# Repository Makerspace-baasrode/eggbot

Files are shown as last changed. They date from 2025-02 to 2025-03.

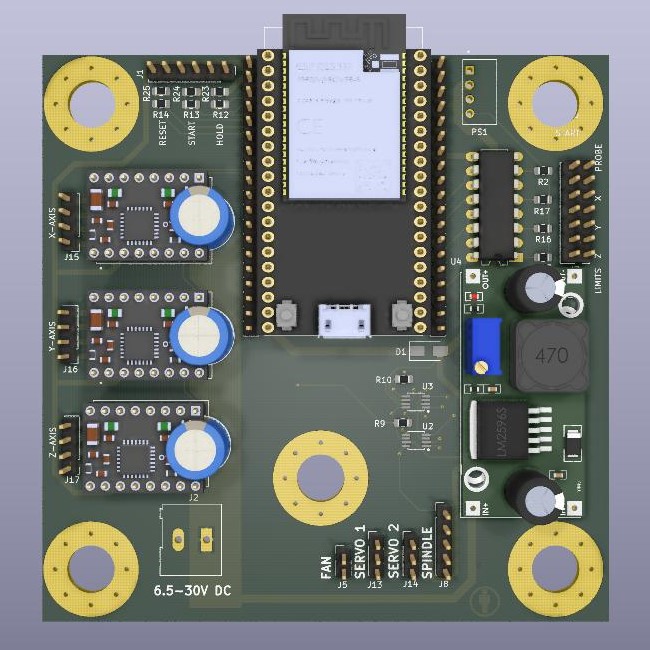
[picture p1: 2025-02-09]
PCB/render/ESP32-cnc.jpg

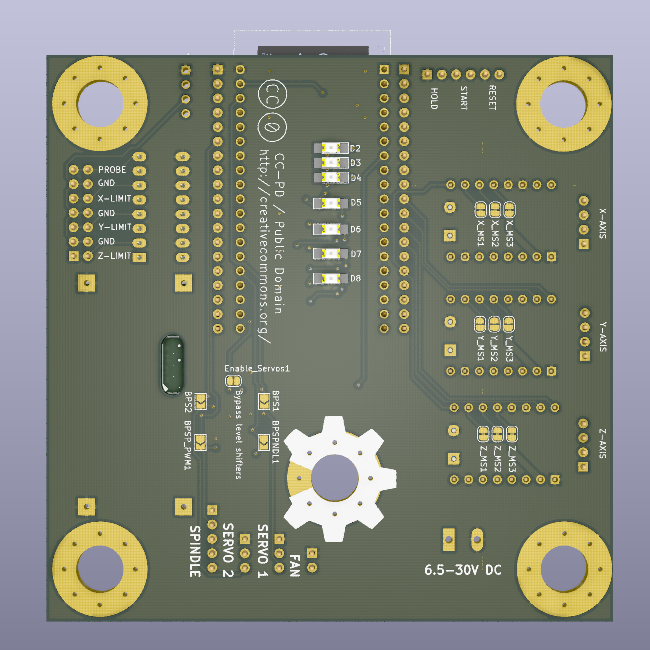
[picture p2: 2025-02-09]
PCB/render/ESP32-cnc_back.png

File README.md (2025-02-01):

# eggbot
a drawing machine using eggs as a canvas

This is a project that started in with a build about 10 years ago.
So in this repository you will find a section of old reference files, of which I can not guarantee that they are still functional. But I rather include them to let you wander around to discover what is our there.
I know that a lot of the software will no longere be functional and needs an update, but I'd liked to keep them here as a reference to what was used 10+ years ago

The new build we are attempting in 2025 will be in the top level. 
It will be structured in the several technices we are going to use, CAD-model, 3D-print, laser cutting, PCB design, PCB assembling, ...

If there is any suggestion to organize it differently please let me know

## original project

this project is a make over of the [Eval Mad Scientists](https://shop.evilmadscientist.com/productsmenu/766) eggbot project. All credits go to them as the originators of the ideas. (https://hackaday.com/2019/04/17/what-can-you-learn-from-an-eggbot/)

## refenced links
### The original
- [The Original Egg-Bot Kit](https://wiki.evilmadscientist.com/The_Original_Egg-Bot_Kit)

### 3D prints
- [Enhanced penholder for SphereBot](https://www.thingiverse.com/thing:13407)
- [Laser Cut Sphere-o-bot](https://www.thingiverse.com/thing:368403#files)
- [Laser Cut Sphere-o-bot Instructables](https://www.instructables.com/Laser-Cut-Sphere-O-Bot/)
- [Fischer Technik Eggbot](https://www.thingiverse.com/thing:8109)
- [Eggcup holders for SphereBot / Completely Printable Eggbot](https://www.thingiverse.com/thing:13960)
- [Completely printable Egg-drawer](https://www.thingiverse.com/thing:7988)
- [Finucane Derivative Eggbot](https://www.thingiverse.com/thing:65753)

### Drawing
- [StippleGen](https://wiki.evilmadscientist.com/StippleGen)
- [StippleGen: Weighted Voronoi](https://www.evilmadscientist.com/2012/stipplegen-weighted-voronoi-stippling-and-tsp-paths-in-processing/)
- [code and designs](https://github.com/davidbliss/eggbot)

### Software
- [SphereBotSenderProcessing](https://github.com/zaggo/SphereBotSenderProcessing)
- [Eggduino](https://github.com/cocktailyogi/EggDuino/)
- [Eggbotsimulator](https://github.com/gabber1/EggbotSimulator)
- [EBB Commands](https://www.schmalzhaus.com/EBB/EBBCommands.html)

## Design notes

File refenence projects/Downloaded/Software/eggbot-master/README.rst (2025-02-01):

Arduino Eggbot
==============

Reference
---------

- Motor Shield v2:
  http://learn.adafruit.com/adafruit-motor-shield-v2-for-arduino/overview
- Stepper motors: http://www.solarbotics.net/library/pdflib/pdf/motorbas.pdf

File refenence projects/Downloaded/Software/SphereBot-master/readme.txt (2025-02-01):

v0.1

This is the firmware for an EggBot-style SphereBot.
The firmware directly interprets GCode send over the serial port.

There will be more information on the SphereBot at http://pleasantsoftware.com/developer/3d (in the near future...)

!!!!!!!!
This sketch needs the following non-standard libraries (install them in the Arduino library directory):
SoftwareServo: http://www.arduino.cc/playground/ComponentLib/Servo
TimerOne: http://www.arduino.cc/playground/Code/Timer1
!!!!!!!!

Copyright 2011 by Eberhard Rensch <http://pleasantsoftware.com/developer/3d>

This program is free software: you can redistribute it and/or modify
it under the terms of the GNU General Public License as published by
the Free Software Foundation, either version 3 of the License, or
(at your option) any later version.

This program is distributed in the hope that it will be useful,
but WITHOUT ANY WARRANTY; without even the implied warranty of
MERCHANTABILITY or FITNESS FOR A PARTICULAR PURPOSE.  See the
GNU General Public License for more details.

You should have received a copy of the GNU General Public License
along with this program.  If not, see <http://www.gnu.org/licenses/>

Part of this code is based on/inspired by the Helium Frog Delta Robot Firmware
by Martin Price <http://www.HeliumFrog.com>

To create tags File: ctags --langmap="C++:+.pde" S*

GCode commands:

G90	Absolut modus
G91	Icremental modus:

M300S0	Servo 0 degree
M300S90	Servo 90 degree

M18	Stepper off

G0X0Y40	Rapid movement (pen 0mm, rotation 40mm)
G1X40Y0 Slower movement (pen 40mm, rotation 0mm)
G1Y10F660 Movement with feed 660mm/s (rotation 10mm)

;	Comment
( .. )	Comment

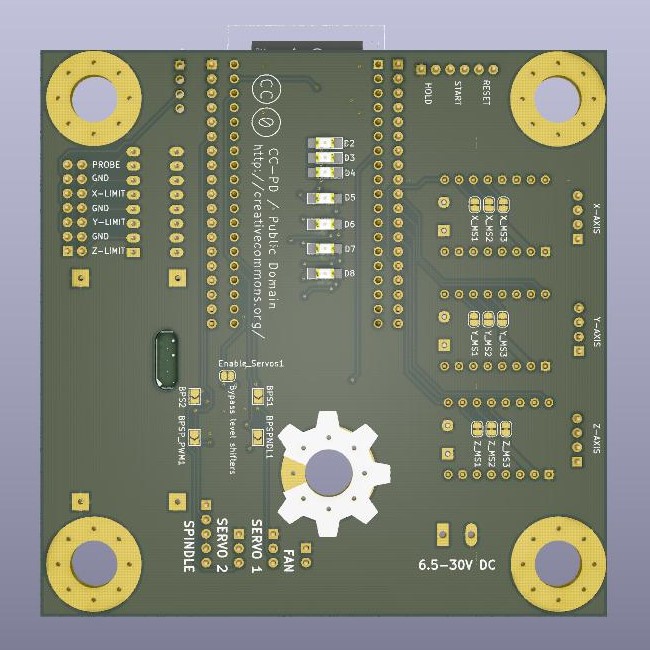
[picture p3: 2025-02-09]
PCB/render/ESP32-cnc_back.jpg

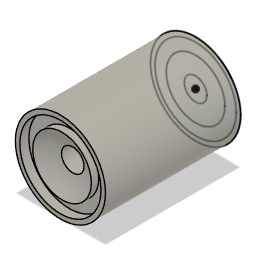
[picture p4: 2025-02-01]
3D CAD model fusion360/_drivecup.a520aff6-5195-480d-919d-d752a0237f96.png

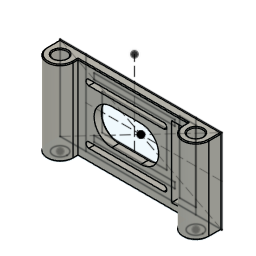
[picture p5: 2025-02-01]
3D CAD model fusion360/_MOTOR BRACKET.0c9dceac-0d53-4d4f-b238-701e19ff46cd.png

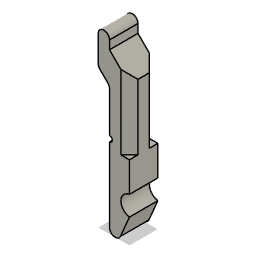
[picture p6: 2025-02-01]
3D CAD model fusion360/_penhouder lever.3cee7135-46d6-436c-b803-6f9b700ddbff.png

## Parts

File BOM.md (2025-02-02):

# BOM

below a bill of materials to build an eggbot.
you still have options to select some of the items. eg. the stepper driver can be any stepper driver with the same footprint as the A4988. 2 types are listed below. You only need 1 type
Cap nuts are included since I like the look of them, but they can be replaced by just normal nuts if you want
O-ring is just and example, if you have 3mm thick o-ring cord you can make them yourself.
The sidepanel can be 3D printed or can be lasercut in acrilyc. That is up to you. The PCB has the same form factor as the sidepanel and can replace 1 of the side panels. If you choose to do so you only need 2 side panels. If you don't like the idea you have to have 3 side panels and an additional 3x M8-nuts
The bearinghouses can be equiped with M4 inserts instead of using standard M4 nuts. This is not in the 3D STL file yet, but if you opt to do so then 8 M4 inserts are needed.
Also the pendrive could be equiped with M4 inserts. Again not in the STL files yet.

The links in the table are just examples no endorsment from my part. They can help you start looking for things. (I have no affiliation with Amazon at all, but it comes handy to show what is needed)

|group|item|quantity|link|
| --- | ---- | --- | --- |
|motor hardware||||
||micro sized servo|1|[AZDelivery 5 x Micro Servo Motor 9G](https://www.amazon.nl/AZDelivery-compatibel-Helikopter-Vliegtuigen-Inclusief/dp/B07CZ42862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)
||nema17 stepper motor|2|[5 stuks, Nema 17, bipolair, 42 Ncm, 1,5 A, 42 x 42 x 39 mm](https://www.amazon.nl/STEPPERONLINE-Stappenmotor-connectoren-3D-printer-CNC-freesmachine/dp/B0B38H2ZMR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)
|electronics||||
||ESP32 dev kit|1|[ESP32 DevKit V4 Ontwikkelingskaart](https://www.amazon.nl/Diymore-Ontwikkelingskaart-ESP32-WROOM-Bluetooth-module-microcontroller/dp/B0C2CRRQCL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)
|stepper driver||||
||TMC2208|2|[BIGTREETECH TMC2209 V1.3 Step-motordriver (6 stuks) 2,8 A](https://www.amazon.com.be/-/nl/Youmile-stappenmotordrivers-koellichaam-schroevendraaier-3D-printermoederborden/dp/B0CD75C83P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)
||TMC2209|2|[Set van 6 TMC2209 V1.3 2,8A](https://www.amazon.com.be/-/nl/Youmile-stappenmotordrivers-koellichaam-schroevendraaier-3D-printermoederborden/dp/B0CD76T6LF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)
||A4988|2|[AZDelivery 5 x A4988 Stappenmotor Driver Module met koellichaam](https://www.amazon.nl/AZDelivery-Stappenmotor-koellichaam-compatibel-Inclusief/dp/B083V59HTB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)
||PCB|1||
|nuts and bolts||||
||threaded rods M8x250mm|3||
||threaded rods M6x250mm|1||
||nuts M8|16 or 19||
||Cap nuts M8|6||
||M4 washer|20||
||M4 bolt x 15|10||
||M4 nut|12||
||M4 inserts|10|[Threaded Insert, M4 x 4 x 6 3D Printing Brass Nuts](https://www.amazon.com/Threaded-Printing-Internal-Embedment-Injection/dp/B0D44KYF8G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)
||M4 bolt x 40|1||
||M4 set bolt|1||
||O-ring 15x3|2|[Othmro Nitril Rubber O-ringen 18mm OD 12mm ID 3.1mm Pack van 50](https://www.amazon.nl/Othmro-ringen-Breedte-Metrische-Afdichtende/dp/B08K7BV6FQ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)
||spring 0.8mm ID 7.2mm L=30mm |1|[Qrity 10 stuks compressieveren, drukveer van roestvrij staal, 1,2 x 10 x 40 mm](https://www.amazon.nl/Qrity-compressieveren-roestvrij-ambachtelijke-reparatie/dp/B0D3TT7JVD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)
||bearing 606zz|2|[10 Stuks 606ZZ Afgedicht Kogellager](https://www.amazon.nl/XiKe-606ZZ-Voorgesmeerd-afdichtingen-Diepgroefkogellager/dp/B07JJC9SFK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)
|3D prints||||
||drive cup|1||
||idler cup|1||
||Bearing house M6|2||
||backpanel|1||
||pen drive|1||
||penarm|1||
||penholder|1||
||penholder lever|1||
||penveer|1||
|lasercuts|||
||sidepanels|2 or 3||

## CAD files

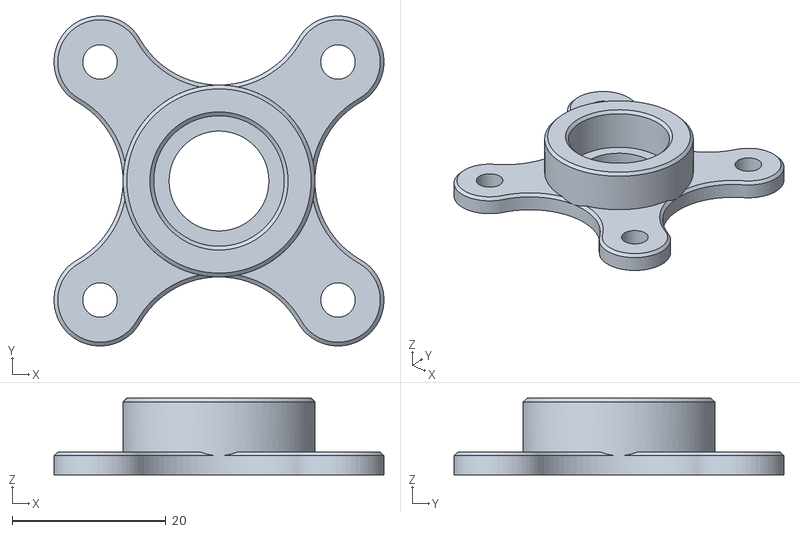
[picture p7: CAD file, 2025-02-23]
3D print models/Bearinghouse M6 V3.stl
43.0 x 43.0 x 10.0

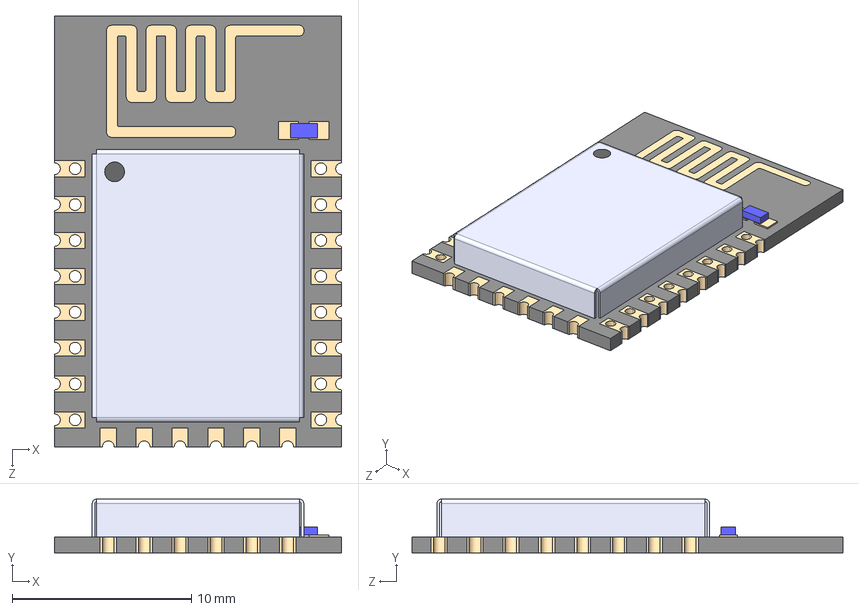
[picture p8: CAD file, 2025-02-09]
PCB/resources/ESP12E/ESP8266-12E_ESP-12E.step
16.0 x 3.00 x 24.0 mm

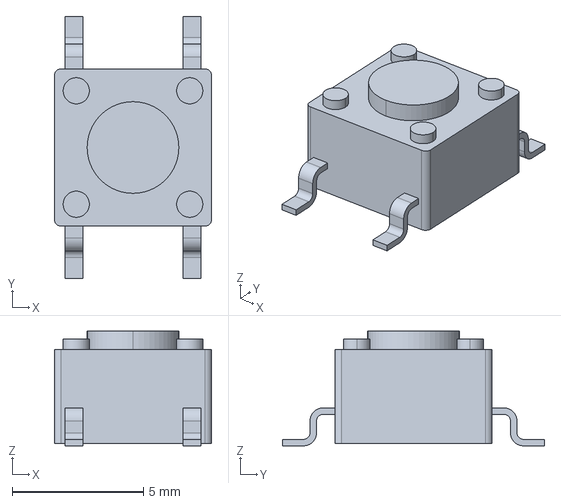
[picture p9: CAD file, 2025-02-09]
PCB/resources/spst-switch/3-1437565-0.step
6.00 x 10.0 x 4.38 mm

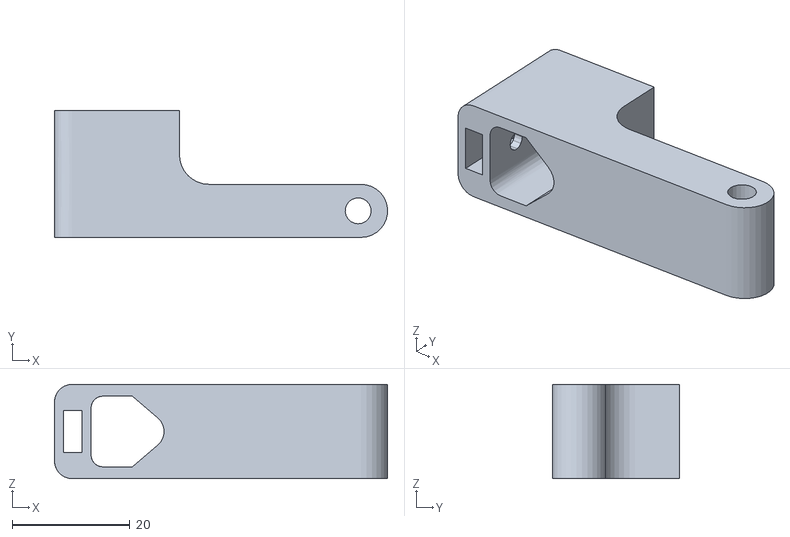
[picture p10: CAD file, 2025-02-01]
refenence projects/Downloaded/Eggbots/Another_spherebot_eggbot_armature/Spherebot_pen.stl
56.5 x 21.5 x 16.0

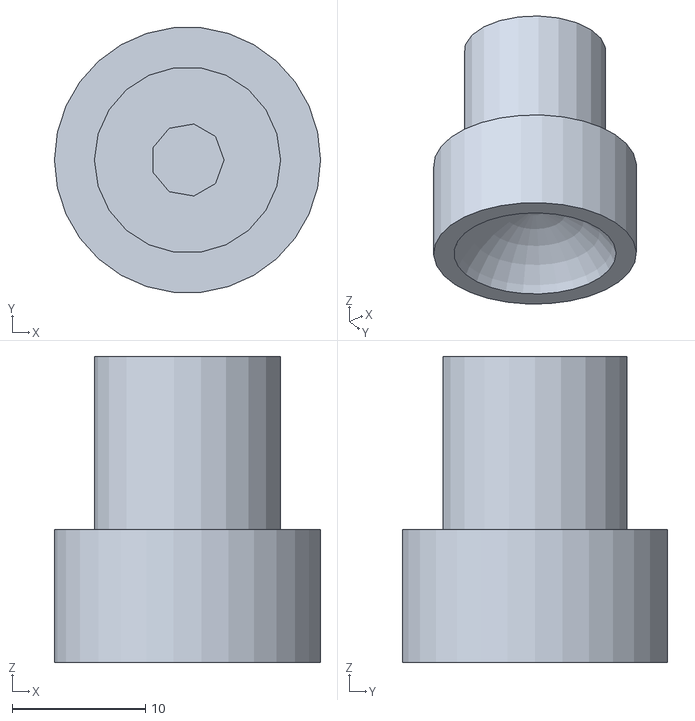
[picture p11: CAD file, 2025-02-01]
refenence projects/Downloaded/Eggbots/Eggcup_holders_for_SphereBot__Completely_Printable_Eggbot/eggcup5mm.stl
20.0 x 19.9 x 23.0

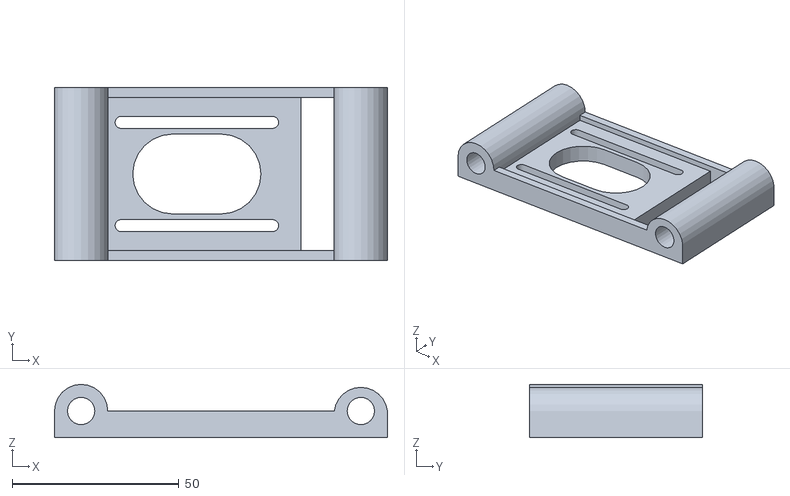
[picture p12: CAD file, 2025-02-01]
refenence projects/Downloaded/Eggbots/Improved_printable_eggbot/back_plate.stl
100.0 x 52.0 x 16.0

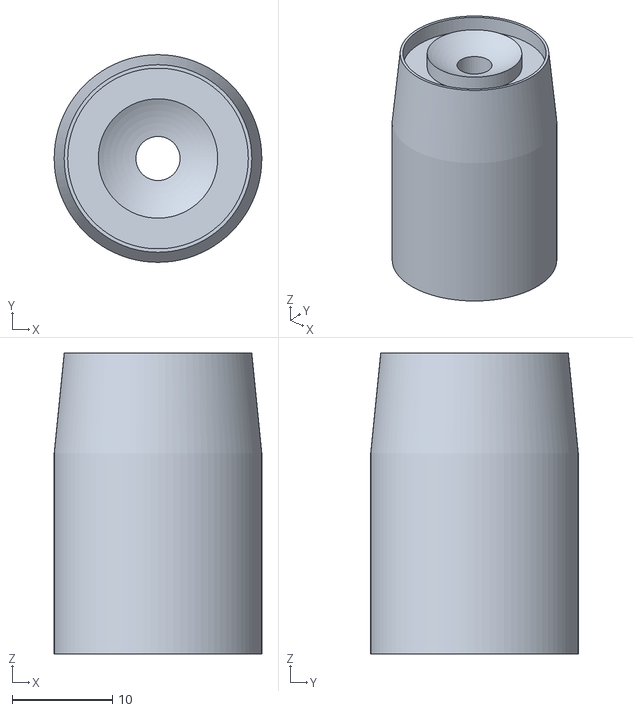
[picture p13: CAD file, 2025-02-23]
3D print models/idler cup V2.stl
20.7 x 20.7 x 30.0

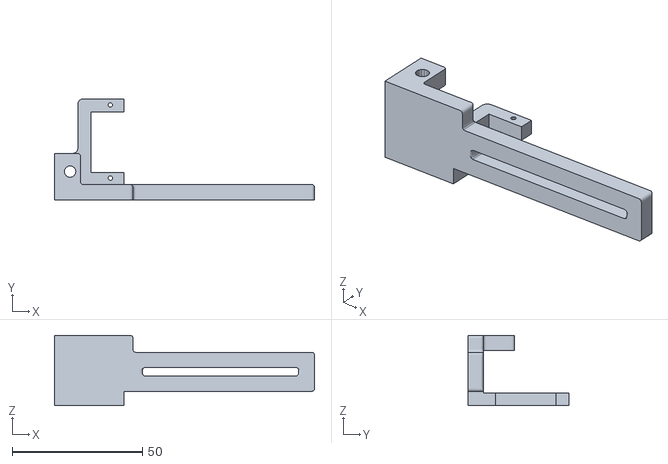
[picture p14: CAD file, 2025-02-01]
refenence projects/Downloaded/Eggbots/Another_spherebot_eggbot_armature/Spherebot_arm.stl
100.0 x 39.0 x 27.0

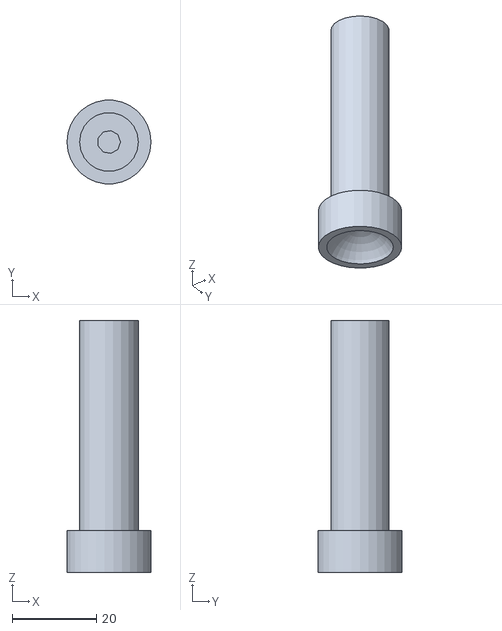
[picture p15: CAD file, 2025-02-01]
refenence projects/Downloaded/Eggbots/Eggcup_holders_for_SphereBot__Completely_Printable_Eggbot/eggcup516.stl
20.0 x 19.9 x 60.0

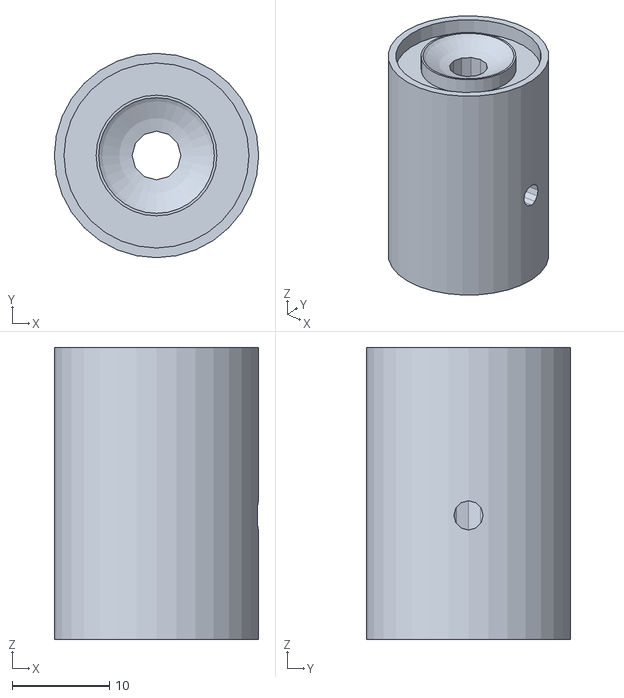
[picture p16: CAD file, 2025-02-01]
refenence projects/Downloaded/Eggbots/Improved_printable_eggbot/drive_cup.stl
21.0 x 21.0 x 30.0

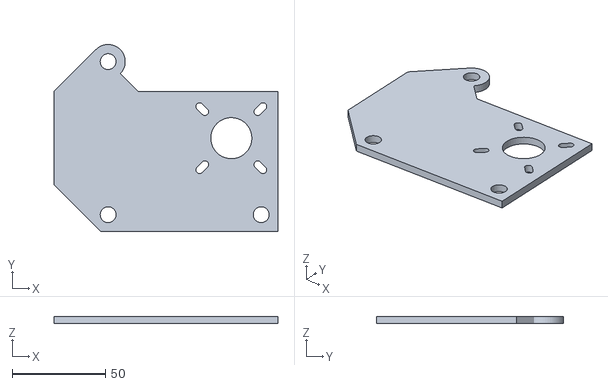
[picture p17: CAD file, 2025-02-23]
3D print models/sidepanel V2.stl
120.0 x 100.2 x 4.00

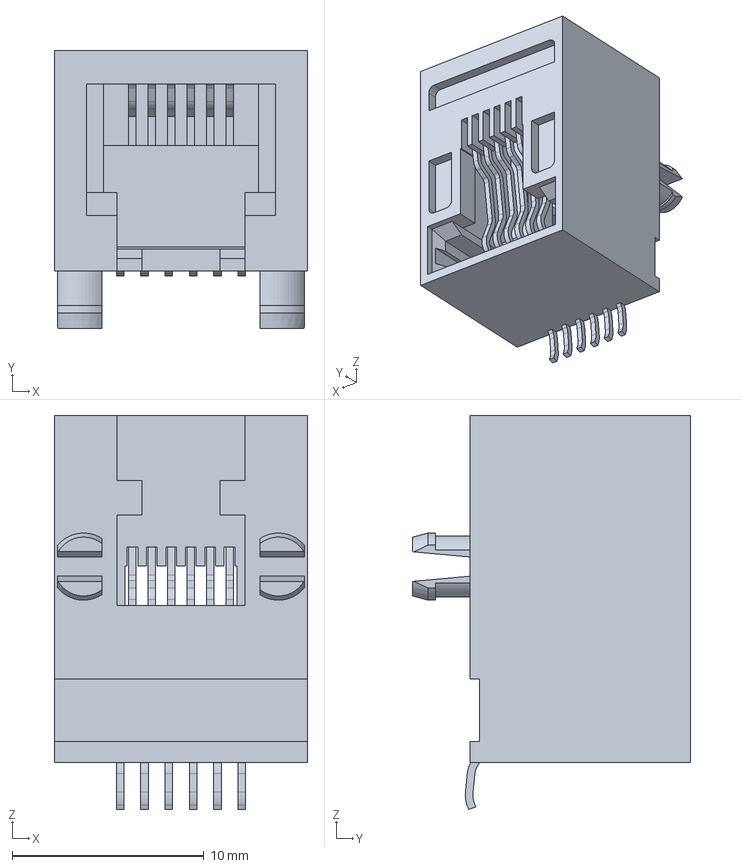
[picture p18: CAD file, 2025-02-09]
PCB/resources/package3d/RJ12.stp
13.2 x 14.5 x 20.6 mm

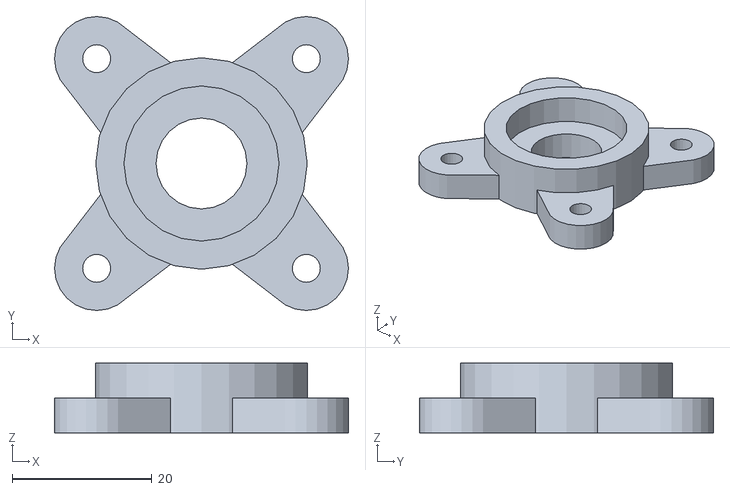
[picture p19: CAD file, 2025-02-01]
refenence projects/Downloaded/Eggbots/Improved_printable_eggbot/idler_bearing_plate.stl
42.1 x 42.1 x 10.0

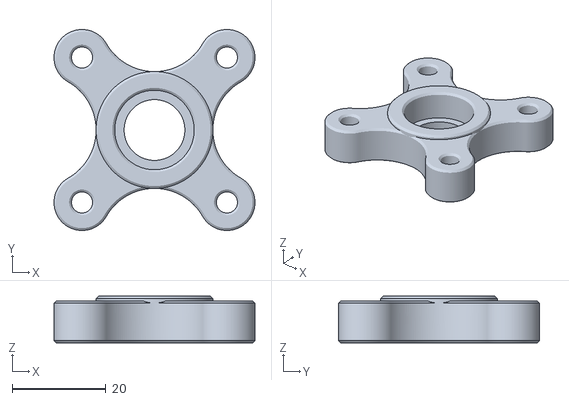
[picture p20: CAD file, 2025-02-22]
3D print models/bearing house M6 inserts V3.stl
43.0 x 43.0 x 10.0

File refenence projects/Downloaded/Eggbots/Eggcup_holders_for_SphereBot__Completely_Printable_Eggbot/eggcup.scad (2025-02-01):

   cupHeight = 10;
   cupDiameter = 20;
   cylDiameter = 14;
   shaftDiameter = 4.9;  // 7.7
   shaftHeight = 50;  // 13
   holeDepth = 10;
   fudge = 0.6;

   difference() {
     cylinder(h = cupHeight, r=cupDiameter/2);
     translate([0,0,-0.4*cupDiameter/2]) { sphere(r=0.9*cupDiameter/2); }
   }
   translate([0,0,cupHeight]) {
   difference() {
       cylinder(h = shaftHeight, r=cylDiameter/2);
       translate([0,0,shaftHeight-holeDepth]) { cylinder(h = shaftHeight+2, r=(shaftDiameter+fudge)/2); }
   }
   }

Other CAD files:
PCB/resources/package3d/8-1437565-0.step
refenence projects/Downloaded/Eggbots/Improved_printable_eggbot/pen_arm_top.stl
3D print models/drivecup_V2.stl
3D CAD model fusion360/BEARINGHOUSE M6 inserts v2.f3d
3D CAD model fusion360/PENDRIVE inserts v1.f3d
3D CAD model fusion360/_BEARINGHOUSE M6.8bb78259-6ec0-4845-8763-fbcfc9640297.f3d
3D CAD model fusion360/_BEARINGHOUSE M8.cff74f27-dfee-4409-ba63-7a86a225738f.f3d
3D CAD model fusion360/_MCMaster.5f8845fe-7c39-4f24-9eef-2dac0d3e2d43.f3d
3D CAD model fusion360/_MOTOR BRACKET.0c9dceac-0d53-4d4f-b238-701e19ff46cd.f3d
3D CAD model fusion360/_PENARM.327dd406-160b-4e44-8dec-6c34584bab60.f3d
3D CAD model fusion360/_PENDRIVE.350a7788-cdd6-4240-858f-49094886f1ab.f3d
3D CAD model fusion360/_SIDEPANEL.0ead6f04-a3f9-46c4-af90-5f052c5ca6cb.f3d
3D CAD model fusion360/_VEER.274ef9a5-93d1-4273-a178-3e04e85e3114.f3d
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

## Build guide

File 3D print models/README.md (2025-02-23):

## What do you need to print :

| Qty | filename |
|-----|---|
| 1x | bearing house M6 inserts V3 |
| 1x | Bearinghouse M6 V3 |
| 1x | drivecup_V2 |
| 1x | idler cup V2 |
| 1x | motor bracket V2 |
| 1x | PENARM |
| 1x | pendrive inserts V2 |
| 1x | penhouder arm |
| 1x | penhouder |
| 1x | penveer |

The side panel can be laser cut or 3D printed. If a laser cutter is available I would go for the acrylic laser cut.

| Qty | filename |
|-----|---|
| 2x | sidepanel V2.dxf laser cut |
| 2x | sidepanel V2.stl 3D print |

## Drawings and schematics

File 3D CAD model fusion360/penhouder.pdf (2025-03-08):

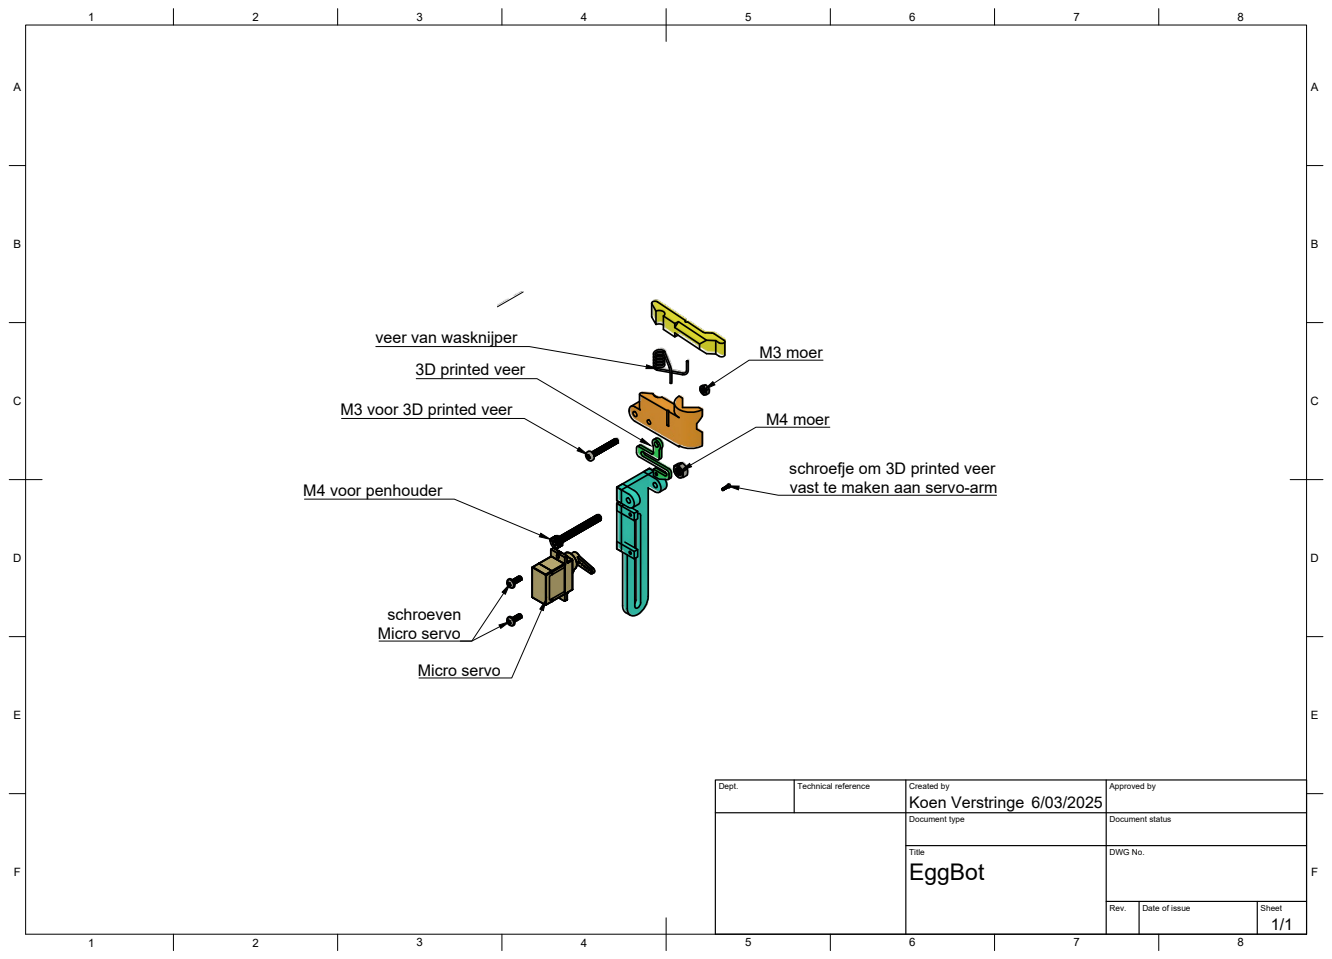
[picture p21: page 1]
Title; DWG No.; Rev.; Date of issue; Sheet; Micro servo; M4 voor penhouder; M3 moer; M4 moer; 3D printed veer

veer van wasknijper

M3 voor 3D printed veer

schroefje om 3D printed veer
vast te maken aan servo-arm

Dept. | Technical reference | Created by Koen Verstringe 6/03/2025 | Approved by

Document type | Document status

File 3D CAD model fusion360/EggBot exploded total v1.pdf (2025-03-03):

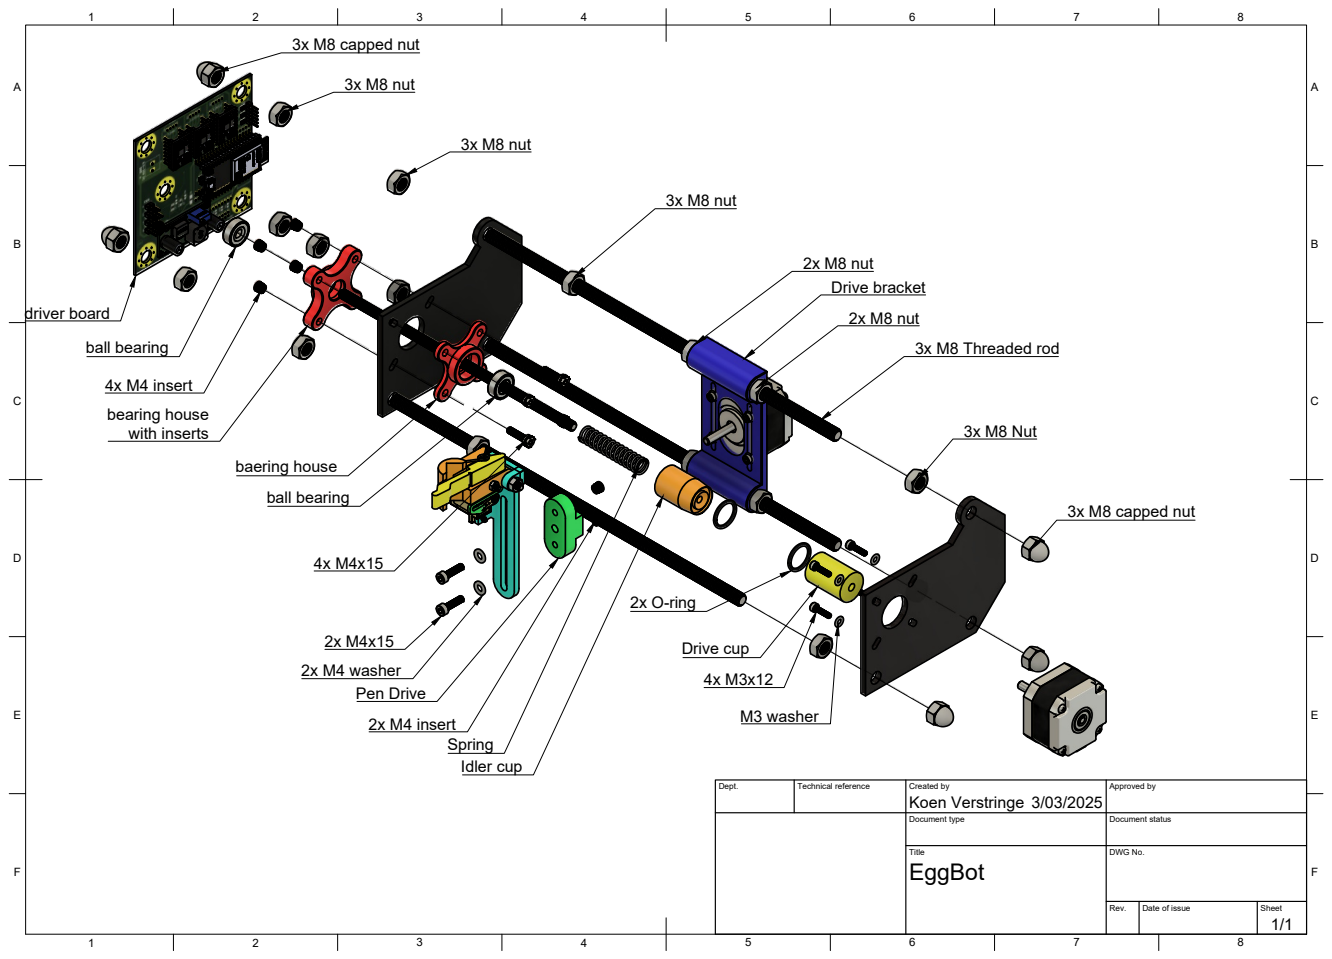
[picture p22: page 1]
Dept.; Technical reference; Created by; Approved by; Document type; Document status; Title; DWG No.; Rev.; Date of issue; Sheet; Koen Verstringe; 3x M8 Nut; 3x M8 capped nut; M3 washer; Drive cup; 2x O-ring; 3x M8 Threaded rod; 2x M4 washer; 2x M4 insert; Pen Drive; 3x M8 nut; 2x M8 nut; Drive bracket; driver board; ball bearing; 4x M4 insert; bearing house with inserts; baering house; Idler cup

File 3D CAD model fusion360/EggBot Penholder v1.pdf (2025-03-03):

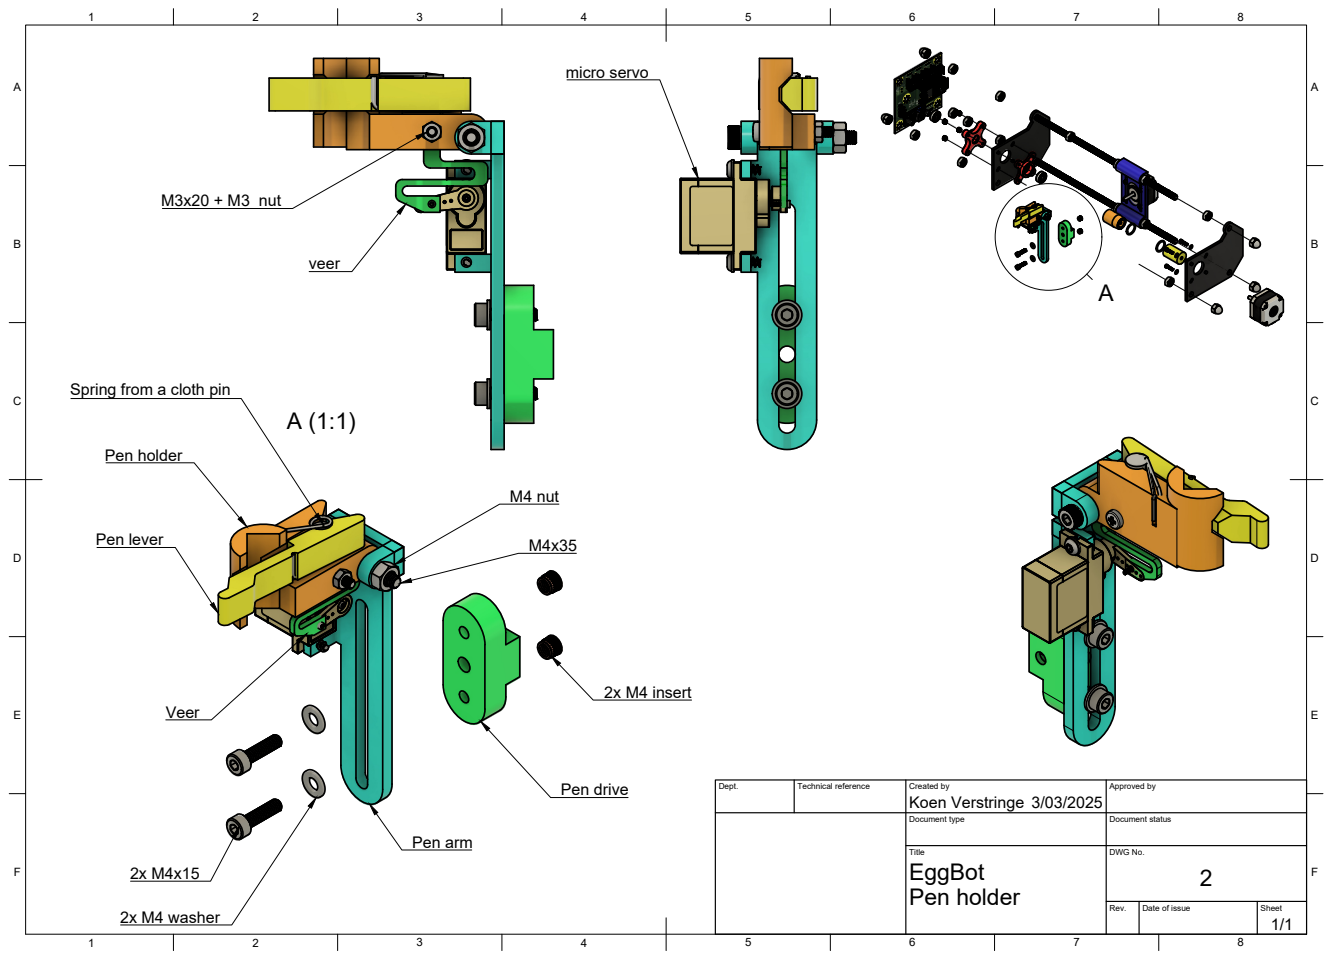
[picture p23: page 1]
Dept.; Technical reference; Created by; Approved by; Document type; Document status; Title; DWG No.; Rev.; Date of issue; Sheet; Pen holder; Koen Verstringe; 2x M4 washer; 2x M4 insert; Pen drive; Pen arm; M4 nut; Pen lever; micro servo; M3x20 + M3 nut

Spring from a cloth pin

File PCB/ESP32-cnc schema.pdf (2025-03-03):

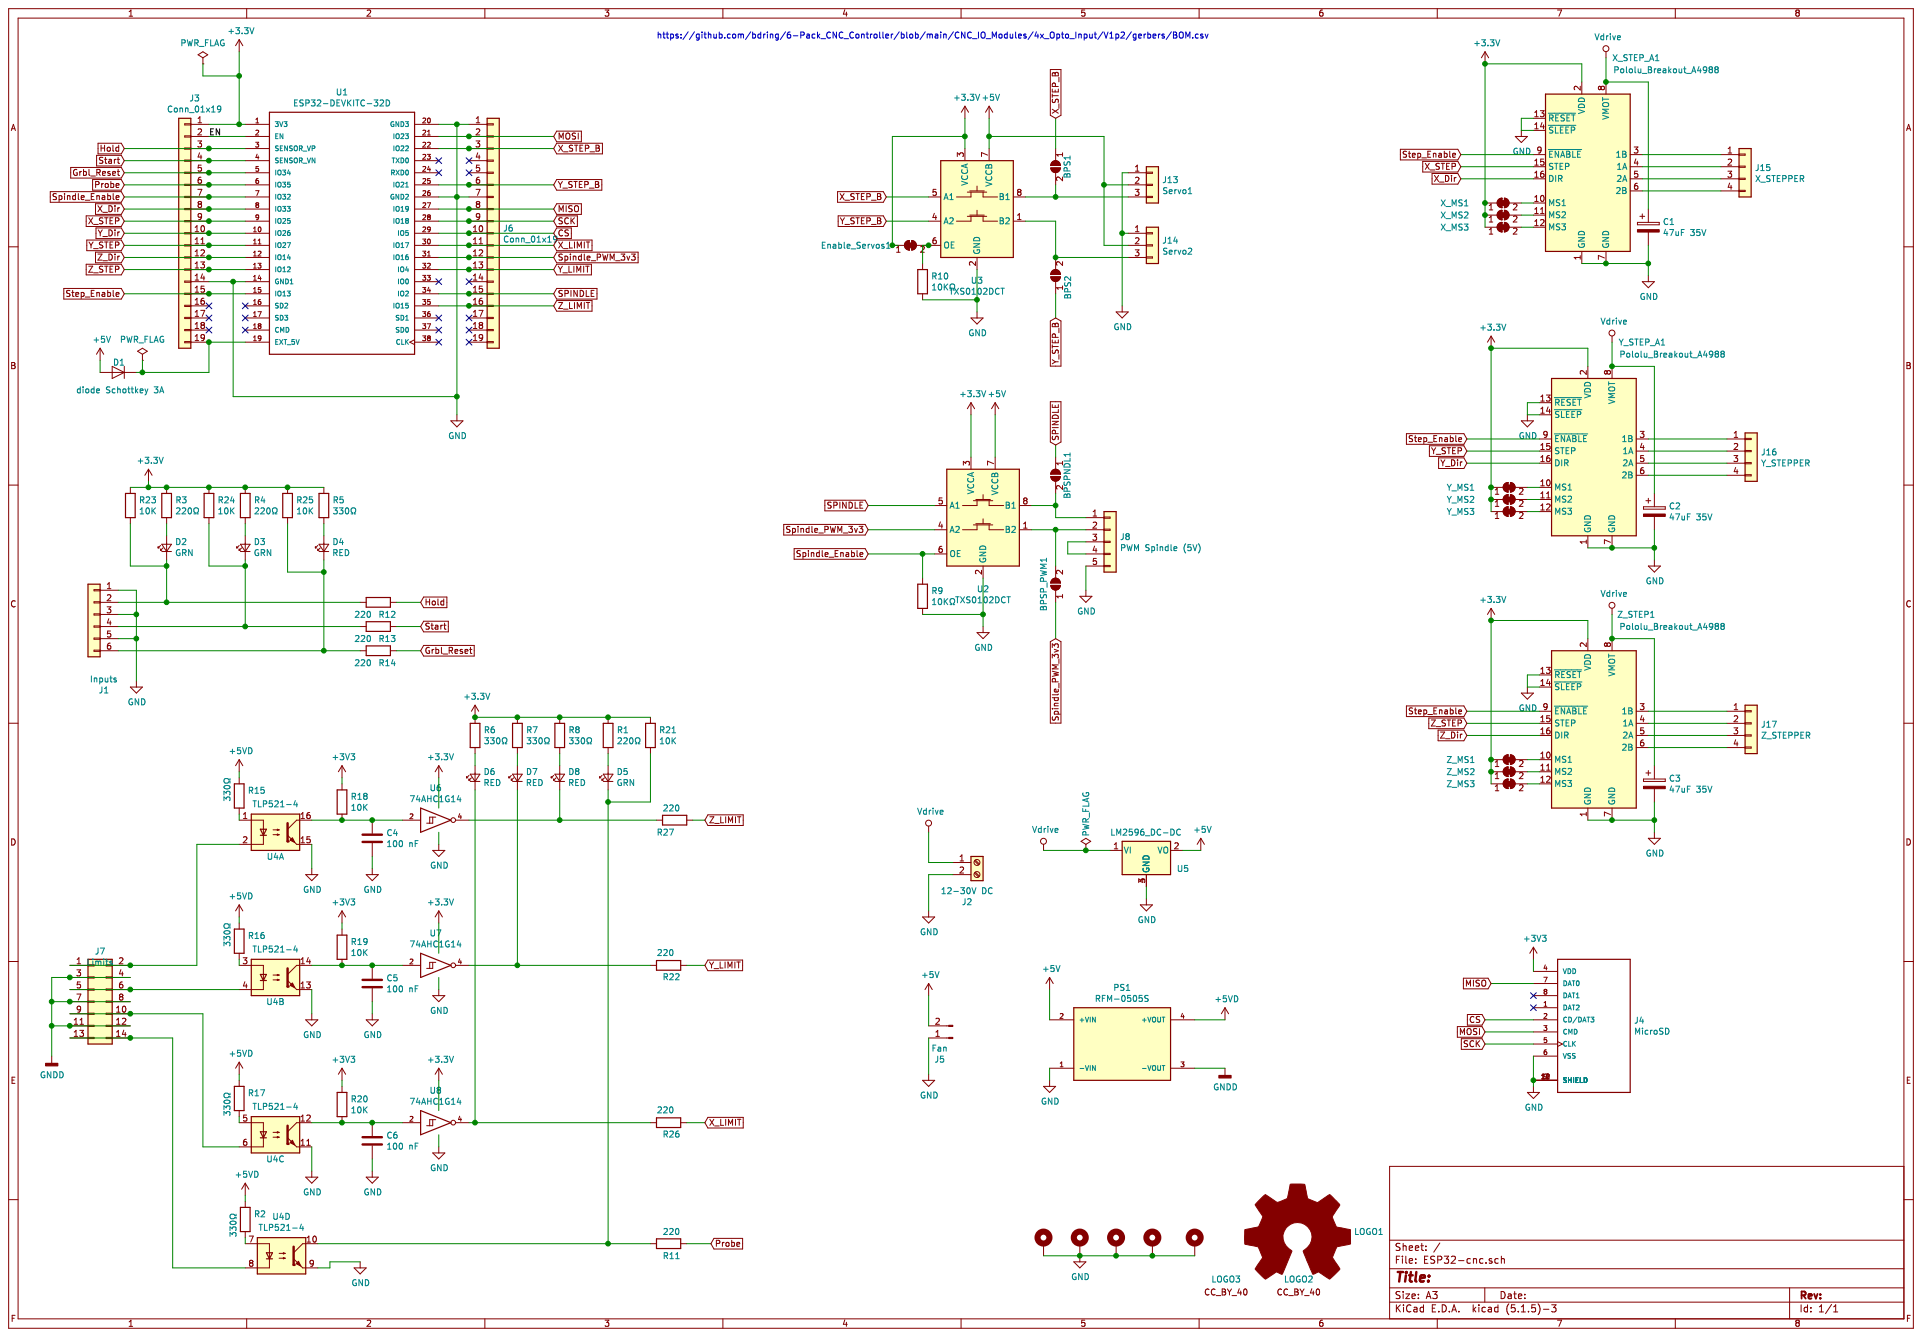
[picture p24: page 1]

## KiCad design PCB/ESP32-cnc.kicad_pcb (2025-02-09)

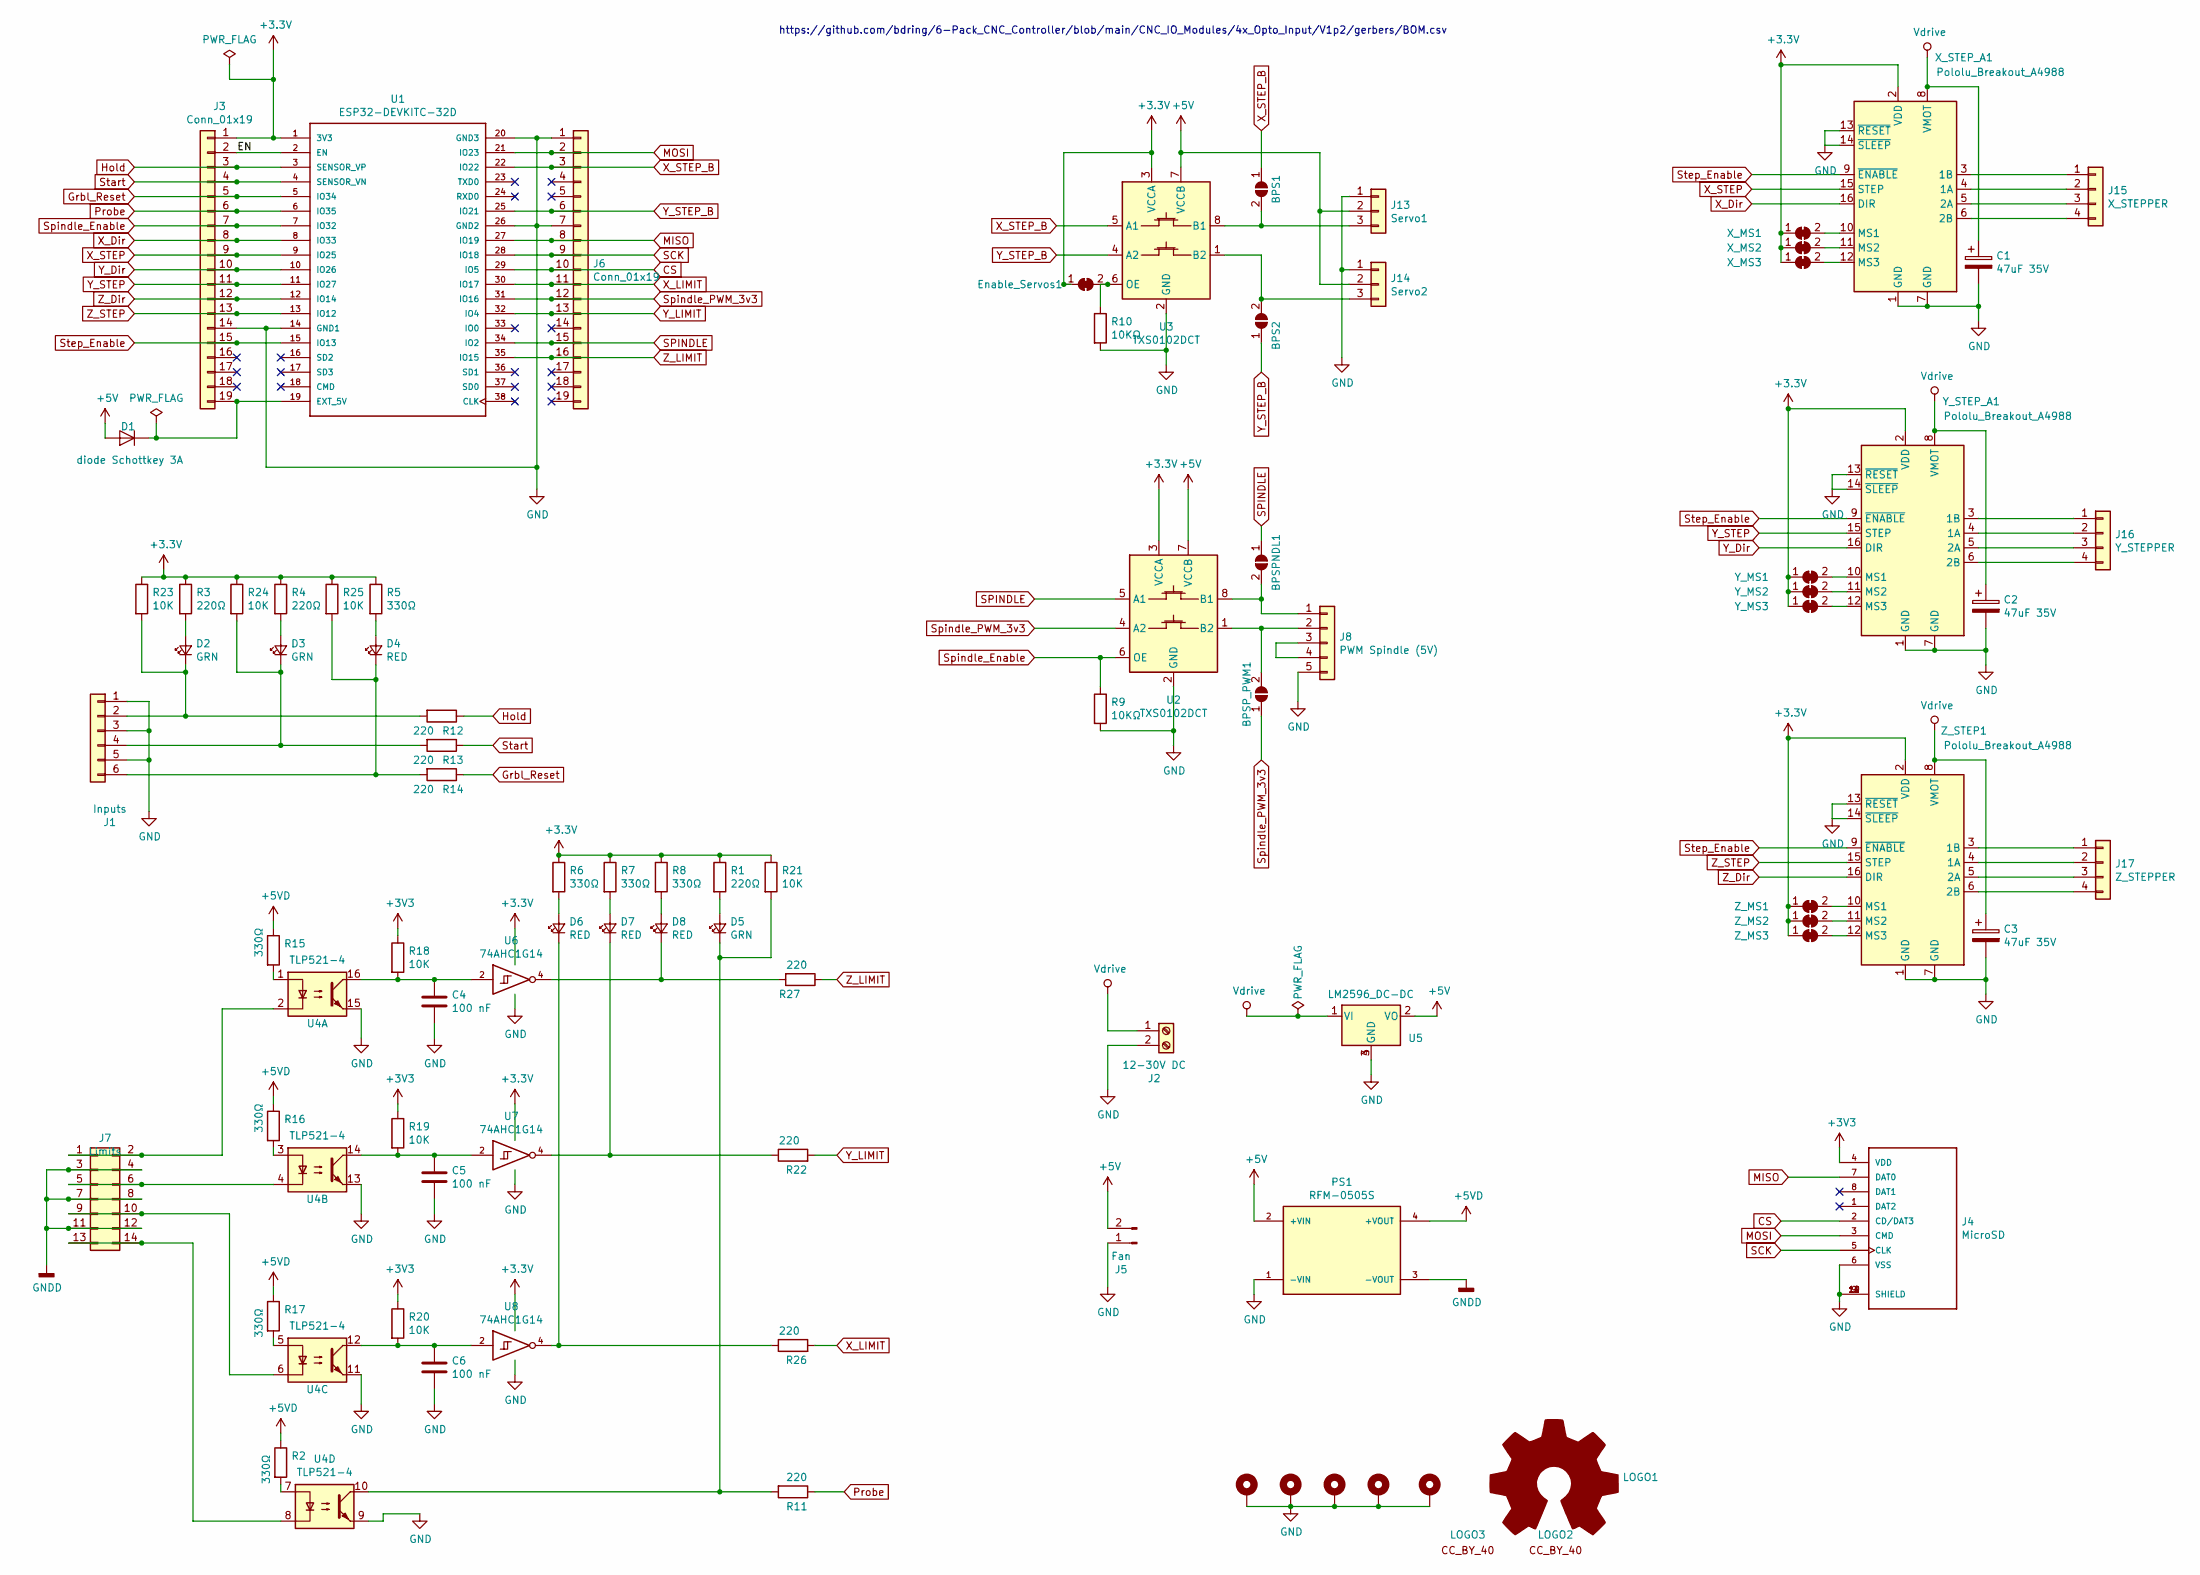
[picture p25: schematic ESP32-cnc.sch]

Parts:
BPS1: SERVO1; SolderJumper-2_P1.3mm_Open_TrianglePad1.0x1.5mm
BPS2: SERVO2; SolderJumper-2_P1.3mm_Open_TrianglePad1.0x1.5mm
BPSPNDL1: SPNDL_ON; SolderJumper-2_P1.3mm_Open_TrianglePad1.0x1.5mm
BPSP_PWM1: SPNDL_PWM; SolderJumper-2_P1.3mm_Open_TrianglePad1.0x1.5mm
C1, C2, C3: 47uF 35V; CP_Radial_D10.0mm_P5.00mm; LCSC C134832
C4, C5, C6: 100 nF; C_0805_2012Metric_Pad1.15x1.40mm_HandSolder
D1: diode Schottkey 3A; D_SMA; LCSC C64982
D2, D3, D5: GRN; LED_1206_HandSoldering
D4, D6, D7, D8: RED; LED_1206_HandSoldering
Enable_Servos1: Enable_Servos; SolderJumper-2_P1.3mm_Bridged_RoundedPad1.0x1.5mm
H1, H2, H3, H4, H5: MountingHole_Pad; MountingHole_8.4mm_M8_Pad_Via
J1: Inputs; PinHeader_1x06_P2.54mm_Vertical
J2: 12-30V DC; TerminalBlock_Altech_AK300-2_P5.00mm
J3, J6: Conn_01x19; PinHeader_1x19_P2.54mm_Vertical
J4: MicroSD; GCT_MEM2067-02-180-00-A_REVB; LCSC C91145
J5: Fan; PinHeader_1x02_P2.54mm_Vertical
J7: Limits; PinHeader_2x07_P2.54mm_Vertical
J8: PWM Spindle (5V); PinHeader_1x05_P2.54mm_Vertical
J13: Servo1; PinHeader_1x03_P2.54mm_Vertical
J14: Servo2; PinHeader_1x03_P2.54mm_Vertical
J15: X_STEPPER; PinHeader_1x04_P2.54mm_Vertical
J16: Y_STEPPER; PinHeader_1x04_P2.54mm_Vertical
J17: Z_STEPPER; PinHeader_1x04_P2.54mm_Vertical
LOGO1: Logo_Open_Hardware_Large; OSHW-Symbol_22.3x20mm_SilkScreen
LOGO2: SYM_CC_BY; Symbol_CreativeCommonsPublicDomain_SilkScreenTop_Small
LOGO3: SYM_CC_BY; Symbol_CC-Attribution_CopperTop_Small
PS1: RFM-0505S; CONV_RFM-0505S; PARTREV 0
R1, R3, R4: 220Ω; R_0805_2012Metric_Pad1.15x1.40mm_HandSolder
R2, R5, R6, R7, R8, R15, R16, R17: 330Ω; R_0805_2012Metric_Pad1.15x1.40mm_HandSolder
R9, R10: 10KΩ; R_0805_2012Metric_Pad1.15x1.40mm_HandSolder; LCSC C140868
R11, R12, R13, R14, R22, R26, R27: 220; R_0805_2012Metric_Pad1.15x1.40mm_HandSolder
R18, R19, R20, R21, R23, R24, R25: 10K; R_0805_2012Metric_Pad1.15x1.40mm_HandSolder
U1: ESP32-DEVKITC-32D; MODULE_ESP32-DEVKITC-32D
U2, U3: TXS0102DCT; SOP65P400X130-8N; LCSC C324082
U4: TLP521-4; DIP-16_W7.62mm_LongPads; lcsc C191333
U5: LM2596_DC-DC; LM2596_DC_DC_Step_Down_Module
U6, U7, U8: 74AHC1G14; SOT-23-5
X_MS1: X_MS1; SolderJumper-2_P1.3mm_Bridged_RoundedPad1.0x1.5mm
X_MS2: X_MS2; SolderJumper-2_P1.3mm_Bridged_RoundedPad1.0x1.5mm
X_MS3: X_MS3; SolderJumper-2_P1.3mm_Bridged_RoundedPad1.0x1.5mm
X_STEP_A1: Pololu_Breakout_A4988; MODULE_A4988_STEPPER_MOTOR_DRIVER_CARRIER
Y_MS1: Y_MS1; SolderJumper-2_P1.3mm_Bridged_RoundedPad1.0x1.5mm
Y_MS2: Y_MS2; SolderJumper-2_P1.3mm_Bridged_RoundedPad1.0x1.5mm
Y_MS3: Y_MS3; SolderJumper-2_P1.3mm_Bridged_RoundedPad1.0x1.5mm
Y_STEP_A1: Pololu_Breakout_A4988; MODULE_A4988_STEPPER_MOTOR_DRIVER_CARRIER
Z_MS1: Z_MS1; SolderJumper-2_P1.3mm_Bridged_RoundedPad1.0x1.5mm
Z_MS2: Z_MS2; SolderJumper-2_P1.3mm_Bridged_RoundedPad1.0x1.5mm
Z_MS3: Z_MS3; SolderJumper-2_P1.3mm_Bridged_RoundedPad1.0x1.5mm
Z_STEP1: Pololu_Breakout_A4988; MODULE_A4988_STEPPER_MOTOR_DRIVER_CARRIER

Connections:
+5V: D1.2 (A), J5.2, J13.2, J14.2, PS1.2 (+VIN), U2.7 (VCCB), U3.7 (VCCB), U5.2 (VO)
+5VD: PS1.4 (+VOUT), R2.1, R15.1, R16.1, R17.1
/EN: J3.2, U1.2 (EN)
CS: J4.2 (CD/DAT3), J6.10, U1.29 (IO5)
GND: C1.2, C2.2, C3.2, C4.2, C5.2, C6.2, H1.1, H2.1, H3.1, H4.1, H5.1, J1.1, J1.3, J1.5, J2.2, J3.14, J4.6 (VSS), J4.9 (SHIELD), J4.10 (SHIELD), J4.11 (SHIELD), J4.12 (SHIELD), J5.1, J6.1, J6.7, J8.5, J13.1, J14.1, PS1.1 (-VIN), R9.2, R10.2, U1.14 (GND1), U1.20 (GND3), U1.26 (GND2), U2.2 (GND), U3.2 (GND), U4.9, U4.11, U4.13, U4.15, U5.3 (GND), U5.4 (GND), U6.3 (GND), U7.3 (GND), U8.3 (GND), X_STEP_A1.1 (GND), X_STEP_A1.7 (GND), X_STEP_A1.13 (~RESET), X_STEP_A1.14 (~SLEEP), Y_STEP_A1.1 (GND), Y_STEP_A1.7 (GND), Y_STEP_A1.13 (~RESET), Y_STEP_A1.14 (~SLEEP), Z_STEP1.1 (GND), Z_STEP1.7 (GND), Z_STEP1.13 (~RESET), Z_STEP1.14 (~SLEEP)
GNDD: J7.3, J7.4, J7.7, J7.8, J7.11, J7.12, PS1.3 (-VOUT)
Grbl_Reset: J3.5, R14.1, U1.5 (IO34)
Hold: J3.3, R12.1, U1.3 (SENSOR_VP)
MISO: J4.7 (DAT0), J6.8, U1.27 (IO19)
MOSI: J4.3 (CMD), J6.2, U1.21 (IO23)
unnamed: BPS1.2 (B), J13.3, U3.8 (B1)
unnamed: BPS2.2 (B), J14.3, U3.1 (B2)
unnamed: BPSPNDL1.2 (B), J8.1, U2.8 (B1)
unnamed: BPSP_PWM1.2 (B), J8.2, U2.1 (B2)
unnamed: C4.1, R18.2, U4.16, U6.2
unnamed: C5.1, R19.2, U4.14, U7.2
unnamed: C6.1, R20.2, U4.12, U8.2
unnamed: D1.1 (K), J3.19, U1.19 (EXT_5V)
unnamed: D2.1 (K), J1.2, R12.2, R23.2
unnamed: D2.2 (A), R3.2
unnamed: D3.1 (K), J1.4, R13.2, R24.2
unnamed: D3.2 (A), R4.2
unnamed: D4.1 (K), J1.6, R14.2, R25.2
unnamed: D4.2 (A), R5.2
unnamed: D5.1 (K), R11.2, R21.2, U4.10
unnamed: D5.2 (A), R1.2
unnamed: D6.1 (K), R26.1, U8.4
unnamed: D6.2 (A), R6.2
unnamed: D7.1 (K), R22.1, U7.4
unnamed: D7.2 (A), R7.2
unnamed: D8.1 (K), R27.2, U6.4
unnamed: D8.2 (A), R8.2
unnamed: Enable_Servos1.2 (B), R10.1, U3.6 (OE)
unnamed: J7.1, J7.2, U4.2
unnamed: J7.5, J7.6, U4.4
unnamed: J7.9, J7.10, U4.6
unnamed: J7.13, J7.14, U4.8
unnamed: J8.3, J8.4
unnamed: J15.1, X_STEP_A1.3 (1B)
unnamed: J15.2, X_STEP_A1.4 (1A)
unnamed: J15.3, X_STEP_A1.5 (2A)
unnamed: J15.4, X_STEP_A1.6 (2B)
unnamed: J16.1, Y_STEP_A1.3 (1B)
unnamed: J16.2, Y_STEP_A1.4 (1A)
unnamed: J16.3, Y_STEP_A1.5 (2A)
unnamed: J16.4, Y_STEP_A1.6 (2B)
unnamed: J17.1, Z_STEP1.3 (1B)
unnamed: J17.2, Z_STEP1.4 (1A)
unnamed: J17.3, Z_STEP1.5 (2A)
unnamed: J17.4, Z_STEP1.6 (2B)
unnamed: R2.2, U4.7
unnamed: R15.2, U4.1
unnamed: R16.2, U4.3
unnamed: R17.2, U4.5
unnamed: X_MS1.2 (B), X_STEP_A1.10 (MS1)
unnamed: X_MS2.2 (B), X_STEP_A1.11 (MS2)
unnamed: X_MS3.2 (B), X_STEP_A1.12 (MS3)
unnamed: Y_MS1.2 (B), Y_STEP_A1.10 (MS1)
unnamed: Y_MS2.2 (B), Y_STEP_A1.11 (MS2)
unnamed: Y_MS3.2 (B), Y_STEP_A1.12 (MS3)
unnamed: Z_MS1.2 (B), Z_STEP1.10 (MS1)
unnamed: Z_MS2.2 (B), Z_STEP1.11 (MS2)
unnamed: Z_MS3.2 (B), Z_STEP1.12 (MS3)
Probe: J3.6, R11.1, U1.6 (IO35)
SCK: J4.5 (CLK), J6.9, U1.28 (IO18)
SPINDLE: BPSPNDL1.1 (A), J6.15, U1.34 (IO2), U2.5 (A1)
Spindle_Enable: J3.7, R9.1, U1.7 (IO32), U2.6 (OE)
Spindle_PWM_3v3: BPSP_PWM1.1 (A), J6.12, U1.31 (IO16), U2.4 (A2)
Start: J3.4, R13.1, U1.4 (SENSOR_VN)
Step_Enable: J3.15, U1.15 (IO13), X_STEP_A1.9 (~ENABLE), Y_STEP_A1.9 (~ENABLE), Z_STEP1.9 (~ENABLE)
Vdrive: C1.1, C2.1, C3.1, J2.1, U5.1 (VI), X_STEP_A1.8 (VMOT), Y_STEP_A1.8 (VMOT), Z_STEP1.8 (VMOT)
X_Dir: J3.8, U1.8 (IO33), X_STEP_A1.16 (DIR)
X_LIMIT: J6.11, R26.2, U1.30 (IO17)
X_STEP: J3.9, U1.9 (IO25), X_STEP_A1.15 (STEP)
X_STEP_B: BPS1.1 (A), J6.3, U1.22 (IO22), U3.5 (A1)
Y_Dir: J3.10, U1.10 (IO26), Y_STEP_A1.16 (DIR)
Y_LIMIT: J6.13, R22.2, U1.32 (IO4)
Y_STEP: J3.11, U1.11 (IO27), Y_STEP_A1.15 (STEP)
Y_STEP_B: BPS2.1 (A), J6.6, U1.25 (IO21), U3.4 (A2)
Z_Dir: J3.12, U1.12 (IO14), Z_STEP1.16 (DIR)
Z_LIMIT: J6.16, R27.1, U1.35 (IO15)
Z_STEP: J3.13, U1.13 (IO12), Z_STEP1.15 (STEP)

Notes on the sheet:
https://github.com/bdring/6-Pack_CNC_Controller/blob/main/CNC_IO_Modules/4x_Opto_Input/V1p2/gerbers/BOM.csv

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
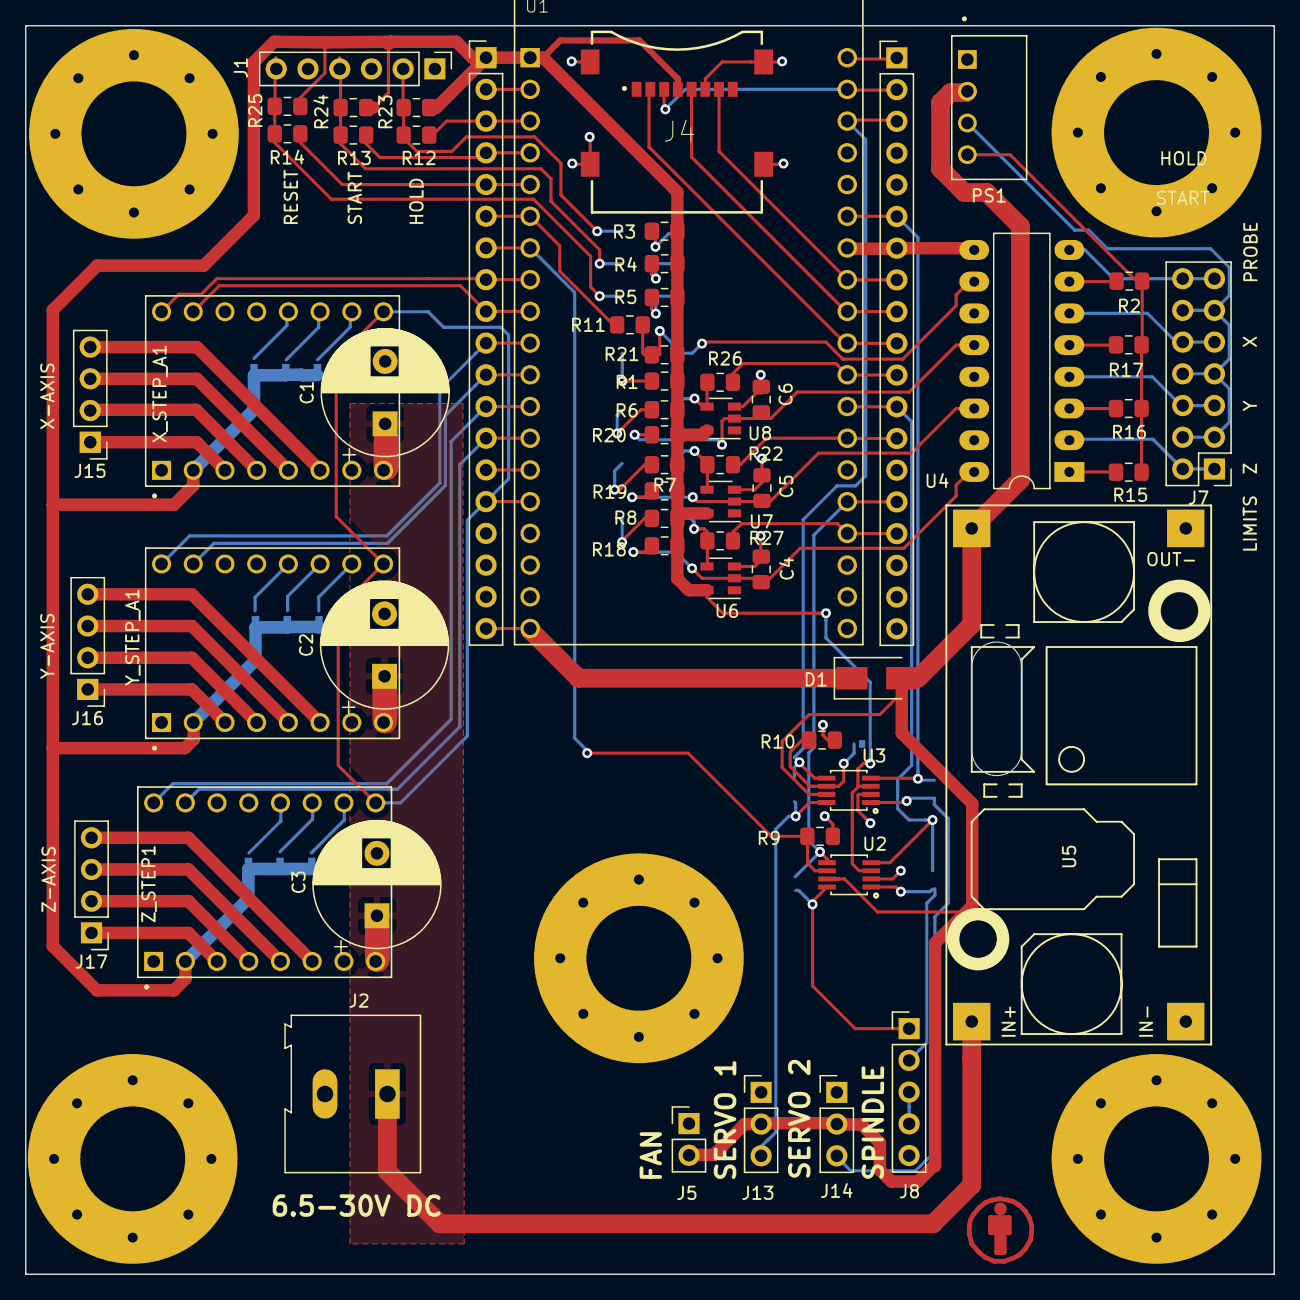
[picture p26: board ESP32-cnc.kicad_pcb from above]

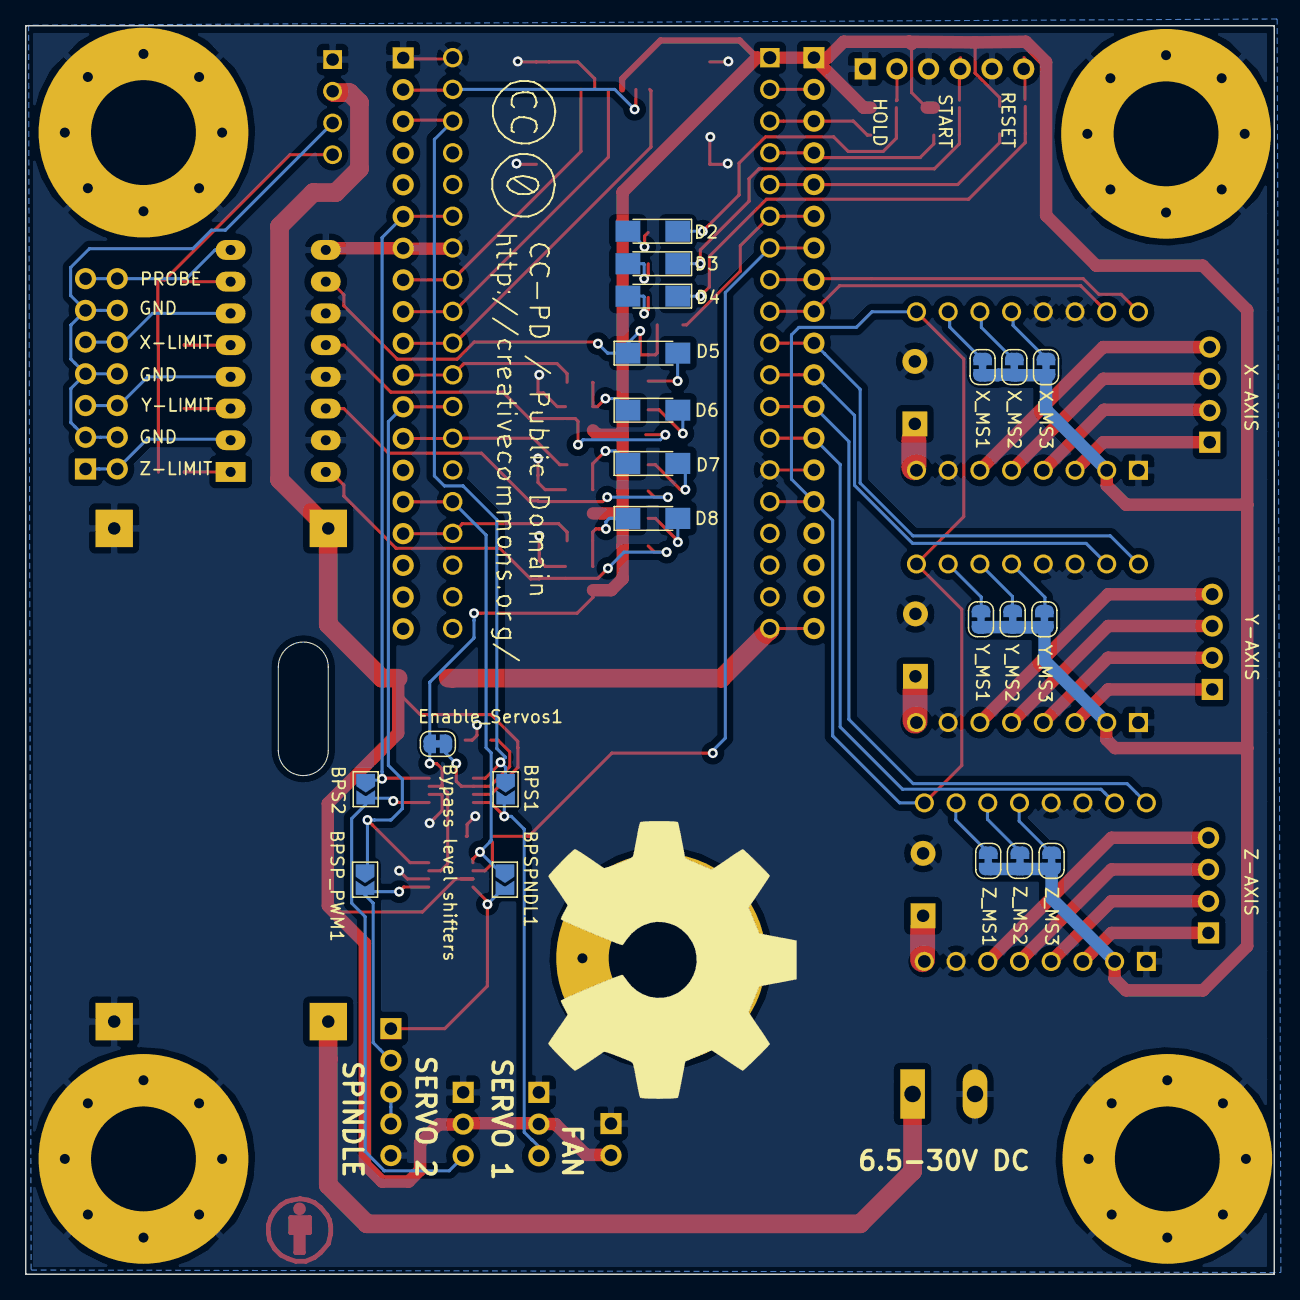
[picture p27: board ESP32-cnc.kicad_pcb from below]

Board: 2 copper layers, 100.0 x 100.0 mm, 88 parts (23 on the bottom side), 83 nets.

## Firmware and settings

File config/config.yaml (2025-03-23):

name: "name: "ESP32 Dev Controller V4-kavers"
board: "ESP32 Dev Controller V4-kavers"

stepping:
  engine: RMT
  idle_ms: 250
  dir_delay_us: 1
  pulse_us: 2
  disable_delay_us: 0


axes:
  shared_stepper_disable_pin: gpio.13
  
  x:
    steps_per_mm: 800
    max_rate_mm_per_min: 2000
    acceleration_mm_per_sec2: 25
    max_travel_mm: 1000
    homing:
      cycle: 2
      mpos_mm: 10
      positive_direction: false
    
    motor0:
      stepstick:
        direction_pin: gpio.33
        step_pin: gpio.25
    motor1:
      null_motor:

  y:
    steps_per_mm: 800
    max_rate_mm_per_min: 2000
    acceleration_mm_per_sec2: 25
    max_travel_mm: 1000
    homing:
      cycle: 2
      mpos_mm: 10
      positive_direction: false

    motor0:
      stepstick:
        direction_pin: gpio.26
        step_pin: gpio.27
    motor1:
      null_motor:

  z:
    steps_per_mm: 100
    max_rate_mm_per_min: 5000
    acceleration_mm_per_sec2: 100
    max_travel_mm: 5
    homing:
      cycle: 1
      mpos_mm: 0
      positive_direction: true

    motor0:
      rc_servo:
        pwm_hz: 50
        output_pin: gpio.22
        min_pulse_us: 1000
        max_pulse_us: 2000

    motor1:
      null_motor:

spi:
  miso_pin: gpio.19
  mosi_pin: gpio.23
  sck_pin: gpio.18

sdcard:
  cs_pin: gpio.5
  card_detect_pin: NO_PIN
       
probe:
  pin: NO_PIN

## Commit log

2025-02-01 reference projects
    added old reference projects
    [EBB_bracket.stl, Spherebot_arm.stl, Spherebot_pen.stl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]
2025-02-01 3D parts
    3D printable and CAD model
    [BEARINGHOUSE M6.stl, BEARINGHOUSE M8.stl, Drivecup.stl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]
2025-02-01 renamed CAD directory
    renamed CAD directury
    to reflect the CAD software used
    [_BEARINGHOUSE M6.8bb78259-6ec0-4845-8763-fbcfc9640297.f3d, _BEARINGHOUSE M8.cff74f27-dfee-4409-ba63-7a86a225738f.f3d, _MCMaster.5f8845fe-7c39-4f24-9eef-2dac0d3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]
2025-02-01 closing bracket
2025-02-01 use of inserts
2025-02-02 PCB adjustment
    needed 18mm for mounting holes M8
    [Motor bracket.stl, sidepanel.dxf]
2025-02-09 PCB design
    updated 3D design to purchased parts
    use M4 inserts instead of M4 nuts
    Kicad V5. design of PCB
    [3-1437565-0.step, 8-1437565-0.step, BEARINGHOUSE M6 inserts v2.f3d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]
2025-02-17 speling aangepast
    speling voor motor as aangepast en fout in fusion opgelost
    [Bearing house M6 inserts V2.stl, drive cup V2.stl, pendrive inserts V2.stl]
2025-02-20 adjustments
    adjustments
    [motor bracket V2.stl]
2025-02-21 upate naar echte componenten
    [bearing house M6 inserts V3.stl, drivecup_V2.stl, pendrive inserts V2.stl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]
2025-02-23 update 3D print STL files
    [BEARINGHOUSE M6.stl, BEARINGHOUSE M8.stl, Bearing house M6 inserts V2.stl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]
2025-02-23 show print info
